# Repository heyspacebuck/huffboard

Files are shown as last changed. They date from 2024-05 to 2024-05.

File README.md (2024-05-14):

# Huffboard

## A board for the Huffbox

# [Learn about the Huffbox HERE!](https://huffbox.aliencat.dev/)

This is a first attempt at improving the connections between the control device--a Raspberry Pi 4--and peripherals using the Pi's GPIO (electromagnets, fans, lights, LED matrix). It was designed to be easy to assemble using JLCPCB's assembly service. If you want to order a board through JLC's assembly service, you will need the files found in the `jlcpcb/production_files` directory.

## Software necessary to inspect the design files

- [KiCad 8](https://www.kicad.org/) or a later version compatible with KiCad 8 projects
- To look at the JLCPCB assembly parts used, it helps to have the [KiCad JLCPCB Tools plugin by Bouni](https://github.com/bouni/kicad-jlcpcb-tools)

## Known issues

- Power has to be supplied to the Pi using its regular power cable. I had hoped to power it through the Huffboard, but the Raspberry Pi Foundation's [guidelines on powering a Pi via a hat](https://github.com/raspberrypi/hats/blob/bcc5afd013360c93f258c9e2cd7d7131e5ca659f/backpowering-diagram.png) are literally sketchy, and their recommended parts don't provide enough power to keep the Pi on.
- I don't like how the relays work or the 0Ω resistors being used as configuration pins. Going to change that in the next revision.

## Schematic

[A PDF of the schematic can be found here.](Schematic.pdf)

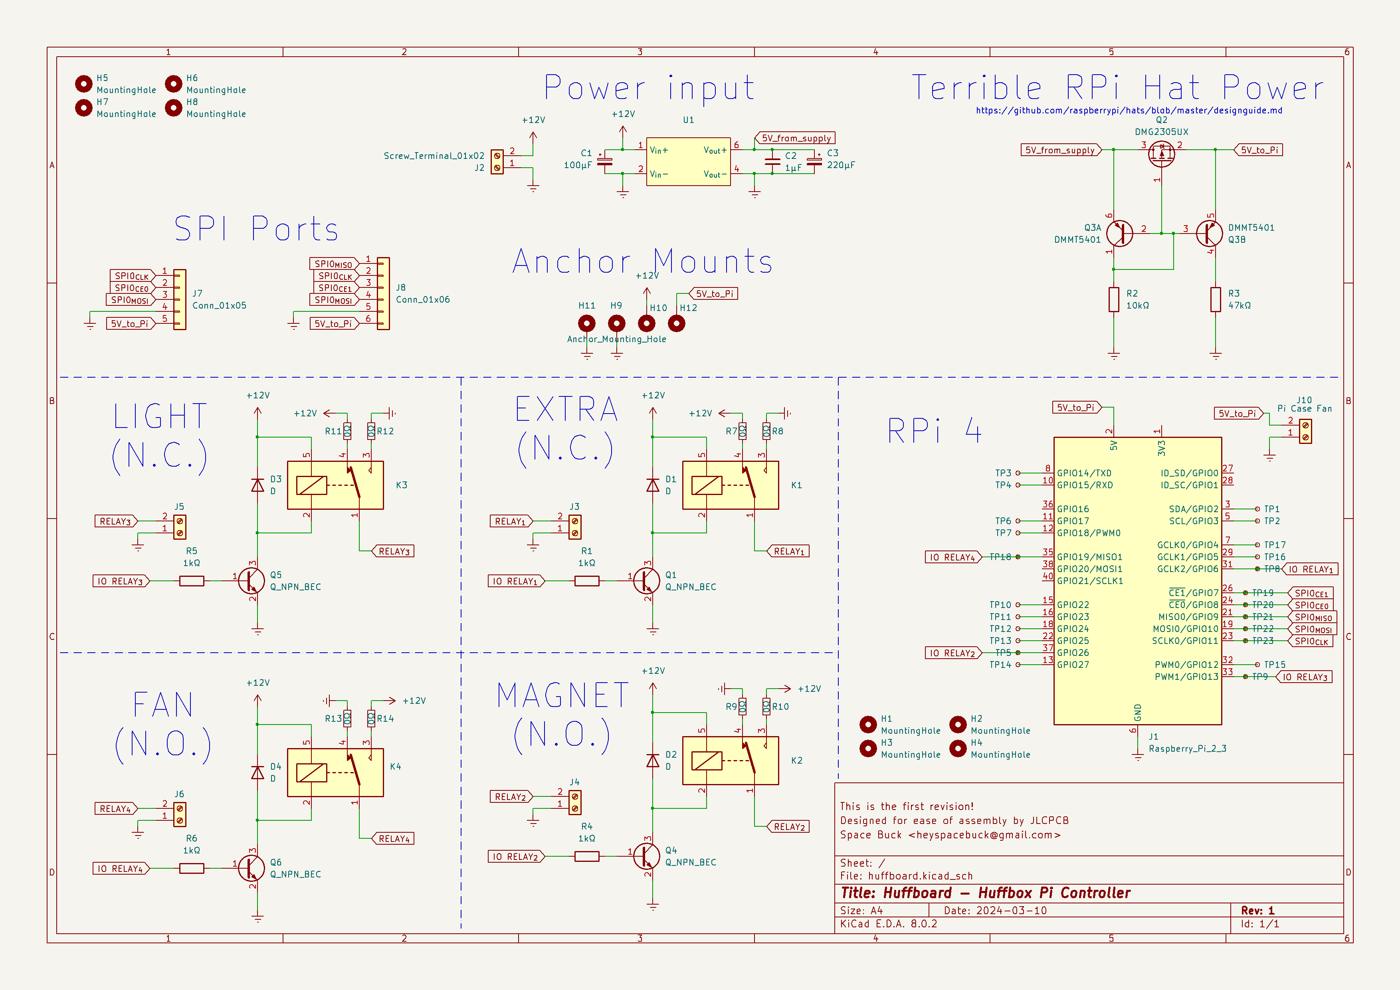
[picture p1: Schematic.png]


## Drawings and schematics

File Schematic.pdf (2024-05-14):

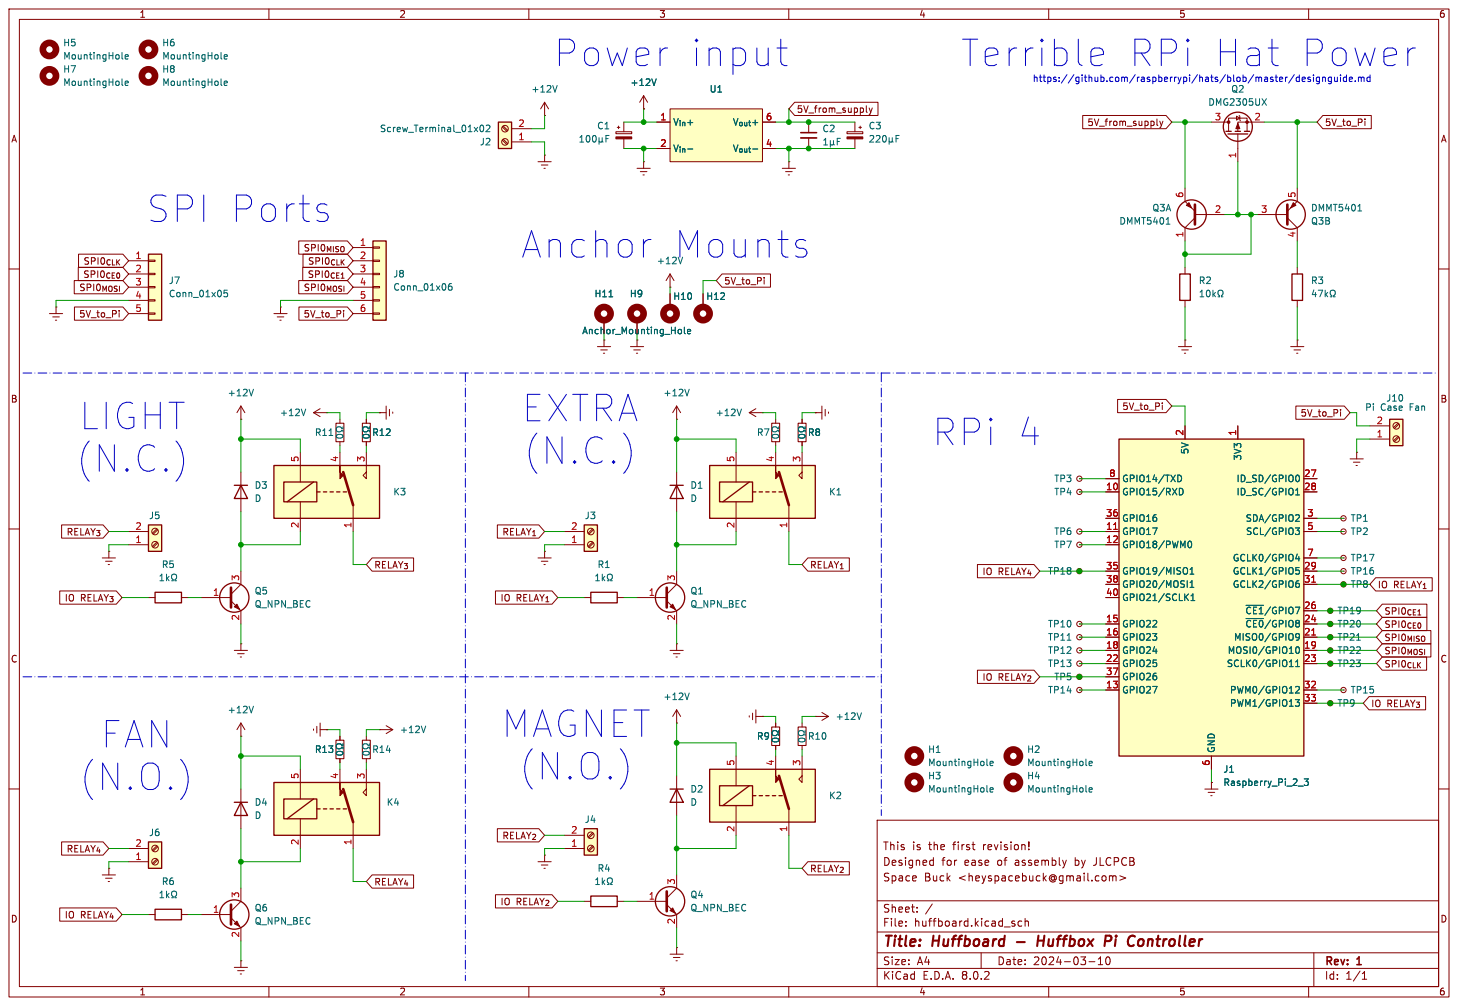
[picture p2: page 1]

Terrible RPi Hat Power

3 K1 H5 MountingHole H8 MountingHole H6 MountingHole H7 MountingHole +12V H9 R12 þÿ0©

https://github.com/raspberrypi/hats/blob/master/designguide.md

This is the first revision!

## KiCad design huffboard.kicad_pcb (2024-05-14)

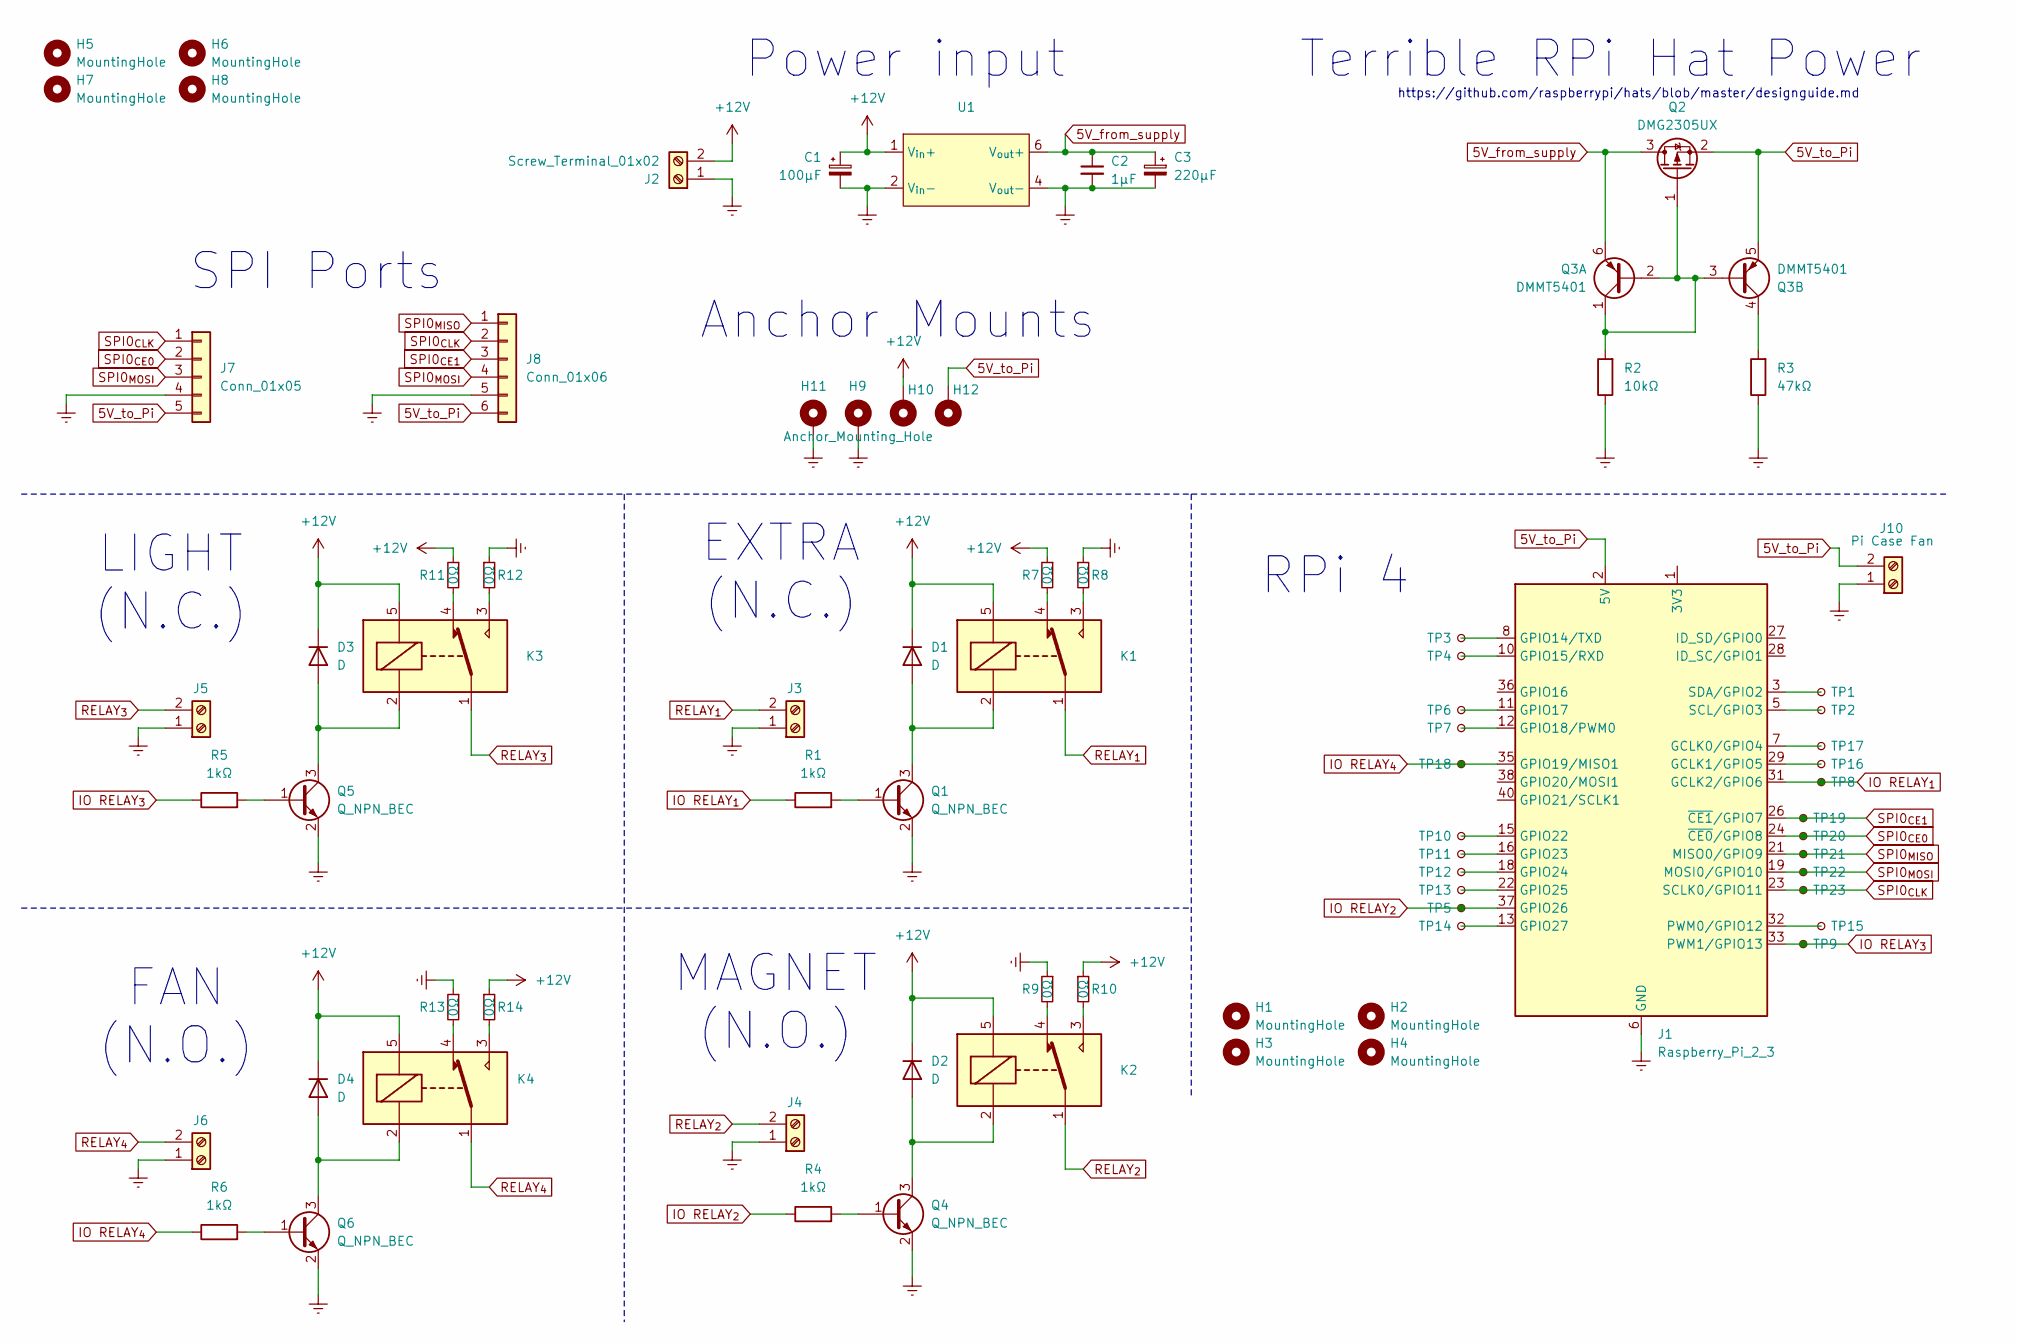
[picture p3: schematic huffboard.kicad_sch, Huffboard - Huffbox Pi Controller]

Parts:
C1: 100μF; CP_Elec_6.3x7.7
C2: 1μF; C_0603_1608Metric
C3: 220μF; CP_Elec_6.3x7.7
D1, D2, D3, D4: D; D_SOD-123F
H1, H2, H3, H4: MountingHole; SMTSO2545CTJ
H5, H6, H7, H8: MountingHole; MountingHole_3.2mm_M3
H9, H10, H11, H12: Anchor_Mounting_Hole; MountingHole_3.2mm_M3_Pad_Via
J1: Raspberry_Pi_2_3; IDC-Header_2x20_P2.54mm_Vertical
J2: Screw_Terminal_01x02; Terminal_Screw_7.62
J3, J4, J5, J6: Screw_Terminal_01x02; TerminalBlock_Phoenix_MKDS-1,5-2-5.08_1x02_P5.08mm_Horizont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
J7: Conn_01x05; JST_PH_B5B-PH-K_1x05_P2.00mm_Vertical
J8: Conn_01x06; JST_PH_B6B-PH-K_1x06_P2.00mm_Vertical
J10: Pi Case Fan; PinSocket_1x02_P2.54mm_Vertical
K1, K2, K3, K4: SANYOU_SRD_Form_C; Relay_SPDT_SANYOU_SRD_Series_Form_C
Q1, Q4, Q5, Q6: Q_NPN_BEC; SOT-23
Q2: DMG2305UX; SOT-23
Q3: DMMT5401; SOT-23-6
R1, R4, R5, R6: 1kΩ; R_0603_1608Metric
R2: 10kΩ; R_0603_1608Metric
R3: 47kΩ; R_0603_1608Metric
R7, R8, R9, R10, R11, R12, R13, R14: 0Ω; R_1206_3216Metric
TP1, TP2, TP3, TP4, TP5, TP6, TP7, TP8, TP9, TP10, TP11, TP12, TP13, TP14, TP15, TP16, TP17, TP18, TP19, TP20, TP21, TP22, TP23: TestPoint_Small; simple_testpoint_pinout
U1: TDK15-XXSXX-MODULE

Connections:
5V_from_supply: C2.1, C3.1, Q2.3 (D), Q3.6 (E1), U1.6 (V_{out}+)
5V_to_Pi: H12.1, J1.2 (5V), J1.4 (5V), J7.5, J8.6, J10.2, Q2.2 (S), Q3.5 (E2)
+12V: C1.1, D1.1 (K), D2.1 (K), D3.1 (K), D4.1 (K), H10.1, J2.2, K1.5, K2.5, K3.5, K4.5, R7.1, R10.1, R11.1, R14.1, U1.1 (V_{in}+)
GNDREF: C1.2, C2.2, C3.2, H9.1, H11.1, J1.6 (GND), J1.9 (GND), J1.14 (GND), J1.20 (GND), J1.25 (GND), J1.30 (GND), J1.34 (GND), J1.39 (GND), J2.1, J3.1, J4.1, J5.1, J6.1, J7.4, J8.5, J10.1, Q1.2 (E), Q4.2 (E), Q5.2 (E), Q6.2 (E), R2.1, R3.1, R8.1, R9.1, R12.1, R13.1, U1.2 (V_{in}-), U1.4 (V_{out}-)
IO RELAY_{1}: J1.31 (GCLK2/GPIO6), R1.1, TP8.1
IO RELAY_{2}: J1.37 (GPIO26), R4.1, TP5.1
IO RELAY_{3}: J1.33 (PWM1/GPIO13), R5.1, TP9.1
IO RELAY_{4}: J1.35 (GPIO19/MISO1), R6.1, TP18.1
unnamed: D1.2 (A), K1.2, Q1.3 (C)
unnamed: D2.2 (A), K2.2, Q4.3 (C)
unnamed: D3.2 (A), K3.2, Q5.3 (C)
unnamed: D4.2 (A), K4.2, Q6.3 (C)
unnamed: J1.1 (3V3), J1.17 (3V3)
unnamed: J1.7 (GCLK0/GPIO4), TP17.1
unnamed: J1.29 (GCLK1/GPIO5), TP16.1
unnamed: J1.8 (GPIO14/TXD), TP3.1
unnamed: J1.10 (GPIO15/RXD), TP4.1
unnamed: J1.11 (GPIO17), TP6.1
unnamed: J1.12 (GPIO18/PWM0), TP7.1
unnamed: J1.15 (GPIO22), TP10.1
unnamed: J1.16 (GPIO23), TP11.1
unnamed: J1.18 (GPIO24), TP12.1
unnamed: J1.22 (GPIO25), TP13.1
unnamed: J1.13 (GPIO27), TP14.1
unnamed: J1.32 (PWM0/GPIO12), TP15.1
unnamed: J1.5 (SCL/GPIO3), TP2.1
unnamed: J1.3 (SDA/GPIO2), TP1.1
unnamed: K1.3, R8.2
unnamed: K1.4, R7.2
unnamed: K2.3, R10.2
unnamed: K2.4, R9.2
unnamed: K3.3, R12.2
unnamed: K3.4, R11.2
unnamed: K4.3, R14.2
unnamed: K4.4, R13.2
unnamed: Q1.1 (B), R1.2
unnamed: Q2.1 (G), Q3.1 (C1), Q3.2 (B1), Q3.3 (B2), R2.2
unnamed: Q3.4 (C2), R3.2
unnamed: Q4.1 (B), R4.2
unnamed: Q5.1 (B), R5.2
unnamed: Q6.1 (B), R6.2
RELAY_{1}: J3.2, K1.1
RELAY_{2}: J4.2, K2.1
RELAY_{3}: J5.2, K3.1
RELAY_{4}: J6.2, K4.1
SPI0_{CE0}: J1.24 (~CE0/GPIO8), J7.2, TP20.1
SPI0_{CE1}: J1.26 (~CE1/GPIO7), J8.3, TP19.1
SPI0_{CLK}: J1.23 (SCLK0/GPIO11), J7.1, J8.2, TP23.1
SPI0_{MISO}: J1.21 (MISO0/GPIO9), J8.1, TP21.1
SPI0_{MOSI}: J1.19 (MOSI0/GPIO10), J7.3, J8.4, TP22.1

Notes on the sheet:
SPI Ports
MAGNET (N.O.)
Anchor Mounts
RPi 4
Terrible RPi Hat Power
FAN (N.O.)
EXTRA (N.C.)
Power input
https://github.com/raspberrypi/hats/blob/master/designguide.md
LIGHT (N.C.)

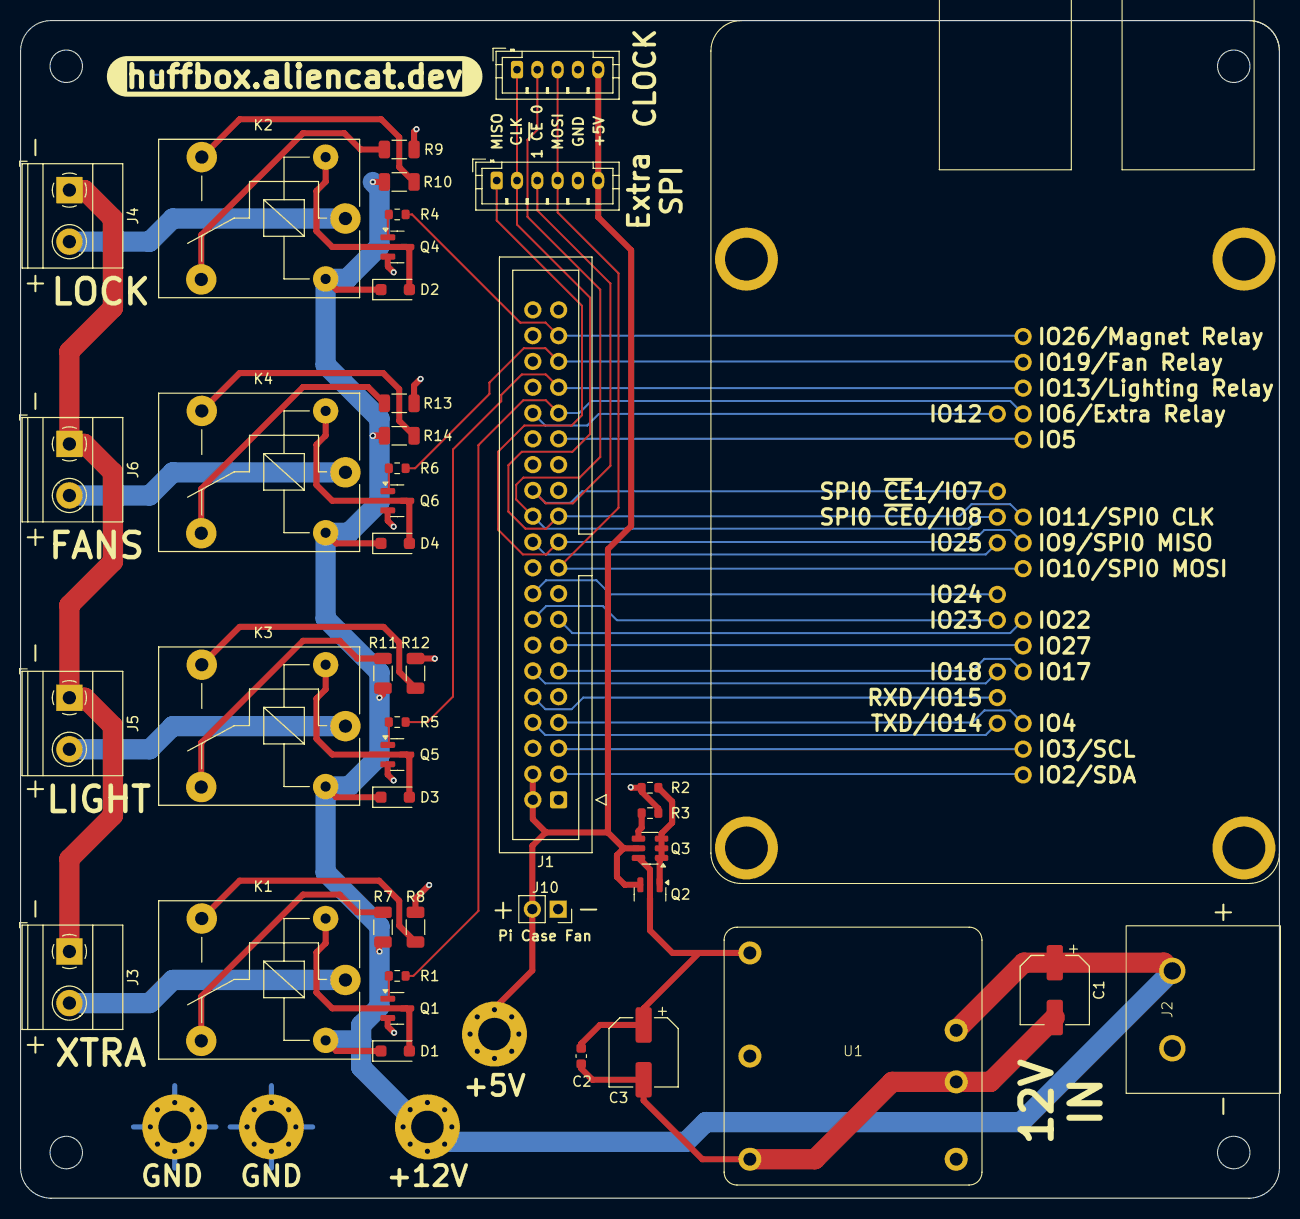
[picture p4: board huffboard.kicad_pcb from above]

Board: 2 copper layers, 124.0 x 116.0 mm, 76 parts (0 on the bottom side), 50 nets.

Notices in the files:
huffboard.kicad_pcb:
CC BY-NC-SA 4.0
